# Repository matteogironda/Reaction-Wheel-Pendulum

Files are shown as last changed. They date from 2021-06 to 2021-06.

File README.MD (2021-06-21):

# This project is intended to be fully open source. For questions feel free to contact me at girondamatteo@gmail.com

## Mechanical Design:

All SolidWorks CAD files are found in the CAD folder. All 3D printed parts are in the STL subdriectory.

### CAD Assembly:

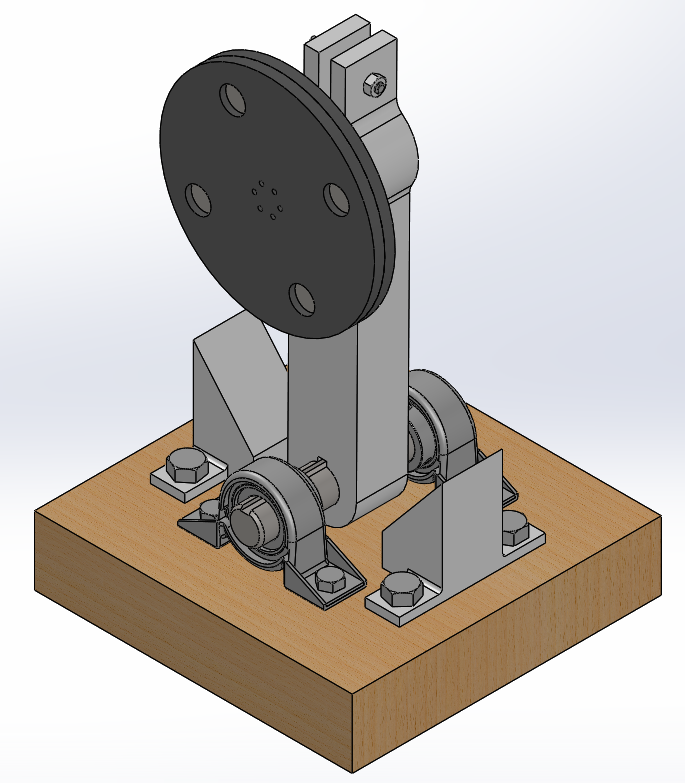
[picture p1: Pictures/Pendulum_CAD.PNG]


### Bill of Materials:

> •	Raspberry Pi (any version with 20 GPIO pins)

> •	Raspberry Pi HAT for DC Motors (https://learn.adafruit.com/adafruit-dc-and-stepper-motor-hat-for-raspberry-pi)

> •	12V DC motor (mine has a max speed of 500 rpm and 1A max)

> •	BNO08x sensor (https://learn.adafruit.com/adafruit-9-dof-orientation-imu-fusion-breakout-bno085/arduino)

> •	9x9x2 in wooden block

> •	Motor attachment to fit with motor shaft (mine had a 6mm shaft https://www.amazon.com/gp/product/B00B887FX8/ref=ppx_yo_dt_b_asin_title_o04_s00?ie=UTF8&psc=1)

> •	Screws for motor attachment (mine were 6x #4-40 x1”)

> •	Keyed 1” Diameter shaft 6” in length

> •	Key (mine was ¼” x ¼”, 1-3/4” long, depends on the keyway of the shaft)

> •	2x Mounted ball bearings for shaft (mounts could theoretically be 3D printed, I bought mine with mounting points)

> •	¼” – 20 thread. 1-1/2” long thumb screw and nut (this is to clamp the motor to the top of the arm)

> •	Self tapping screws for the bearing mounts and side supports (I ended up going with a ½” size, 1-1/2” long; definitely an overkill and not as easy to drive into wood. Make sure you have the appropriate drive bits and socket adapters)

> •	Steel (or metal with similar density) ring (https://www.ebay.com/itm/203450660510)

> •	Access to a 3D printer, soldering iron, appropriate DC power supplies (separate for Pi and motor), connectors, drill, foam, tape.  

### Front View of Pendulum:
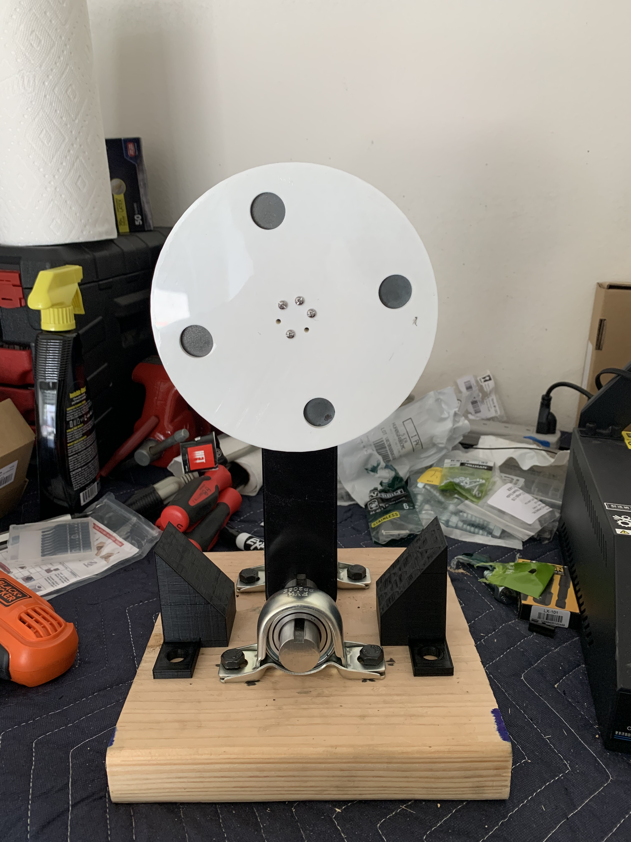
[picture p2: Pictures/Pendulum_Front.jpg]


### Side View of Pendulum:
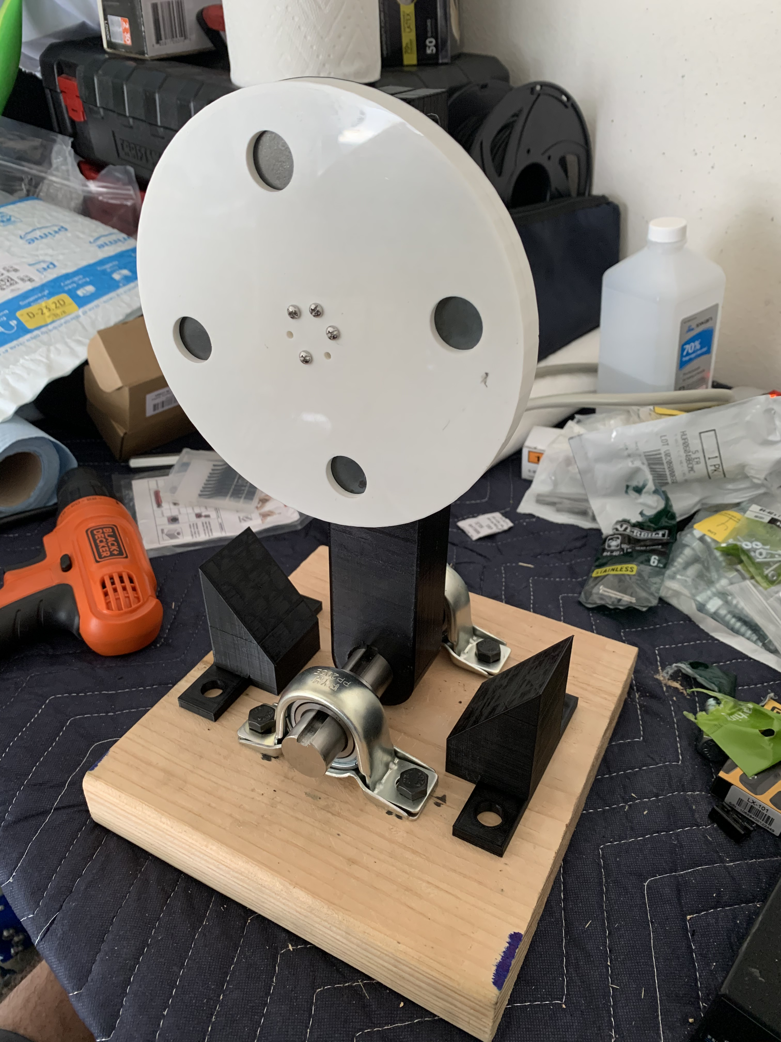
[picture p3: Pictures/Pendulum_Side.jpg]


The mechanical design was inspred by https://www.researchgate.net/publication/331271615_Design_Modeling_and_Control_of_a_Reaction_Wheel_Balanced_Inverted_Pendulum and its authors. 

## Controller

The idea is to send a PWM signal to the motor to rotate the reaction wheel against the motion of the pendulum arm. Gains are tuned to adjust the needed voltage input based on the state vector of the arm. States are updated from the IMU in the feedback loop. The control input becomes saturated at 12V and -12V.

A simulation of the equations of motion and state vector algebra is found in simulation.py. The simulation allows you to change starting conditions and gains, and outputs control effort and states. 

## Notes

I am using UART communication over I2C because the BNO08x series has clock stretching issues when interfacing with the default I2C bus of the pi. This can be worked around by using different SCL and SDA pins on the GPIO that use hardware clock stretching instead of software clock stretching (see https://github.com/adafruit/Adafruit_CircuitPython_BNO08x/issues/7). I found that it's just simpler to use UART for this application, as the motor driver is already using the pi's default I2C bus.

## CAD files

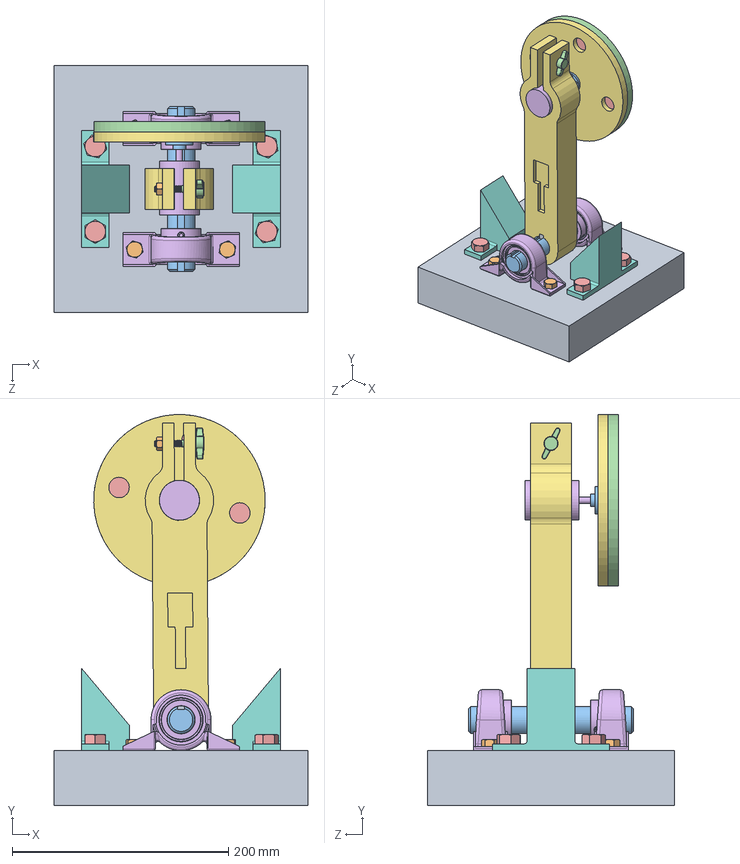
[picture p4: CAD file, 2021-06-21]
CAD/Assembly.SLDASM
235.0 x 361.9 x 228.6 mm
Key
Motor_Nut
Shaft
Thumb_Screw
Wood_Screw x 4
Bearing x 2
Pendulum_Arm
Side_Support x 2
Wooden_Block
Bearing_Wood_Screw x 4
Motor_Mount
Outside_Wheel_Mount
Reaction_Wheel
Motor
Motor_Side_Wheel_Mount

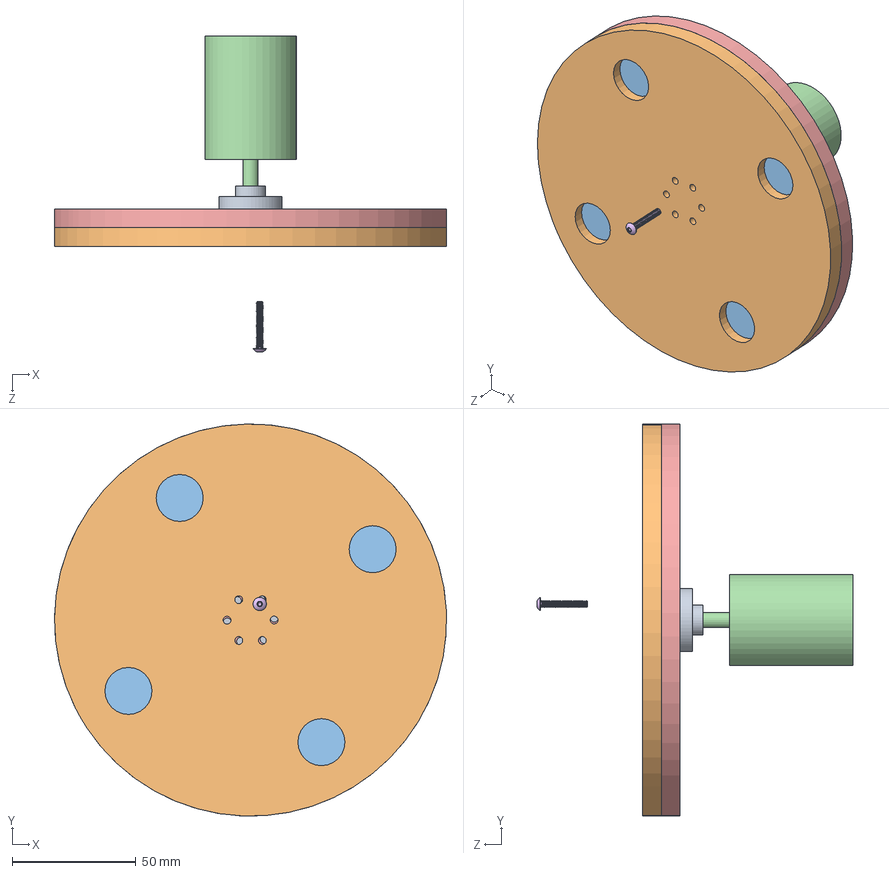
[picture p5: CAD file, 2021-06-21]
CAD/Wheel_Assembly.SLDASM
158.7 x 158.7 x 128.0 mm
Motor_Mount
Outside_Wheel_Mount
Reaction_Wheel
Motor
Motor_Side_Wheel_Mount
Wheel_Screw

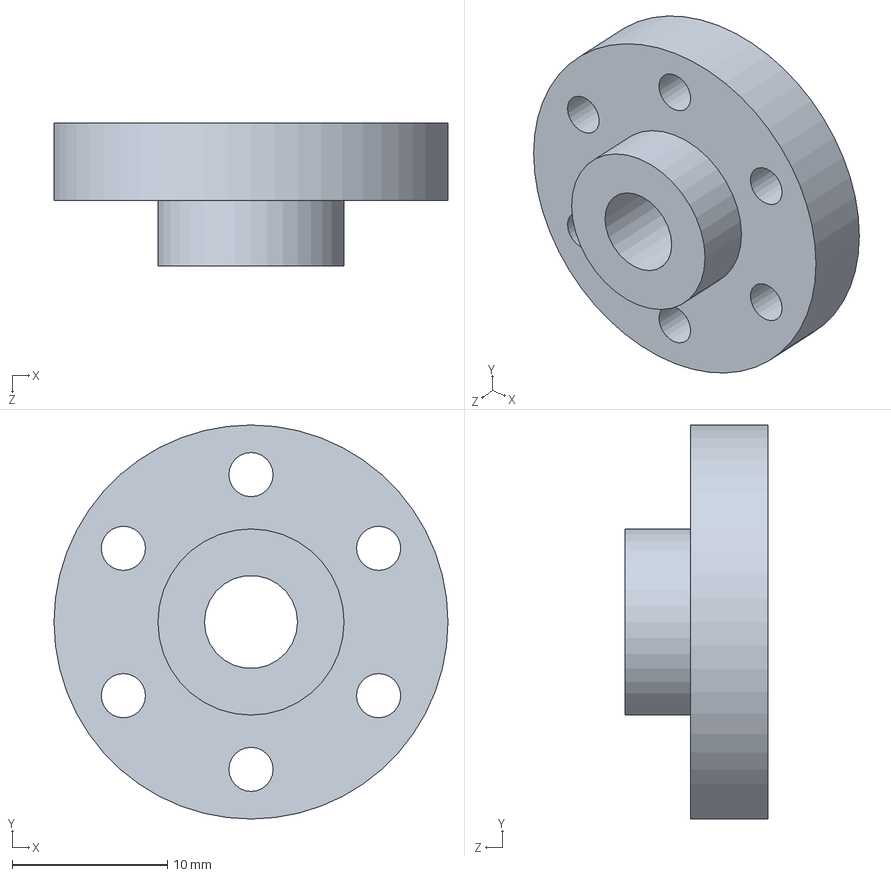
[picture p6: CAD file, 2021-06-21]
CAD/Motor_Mount.SLDPRT
25.4 x 25.4 x 9.20 mm

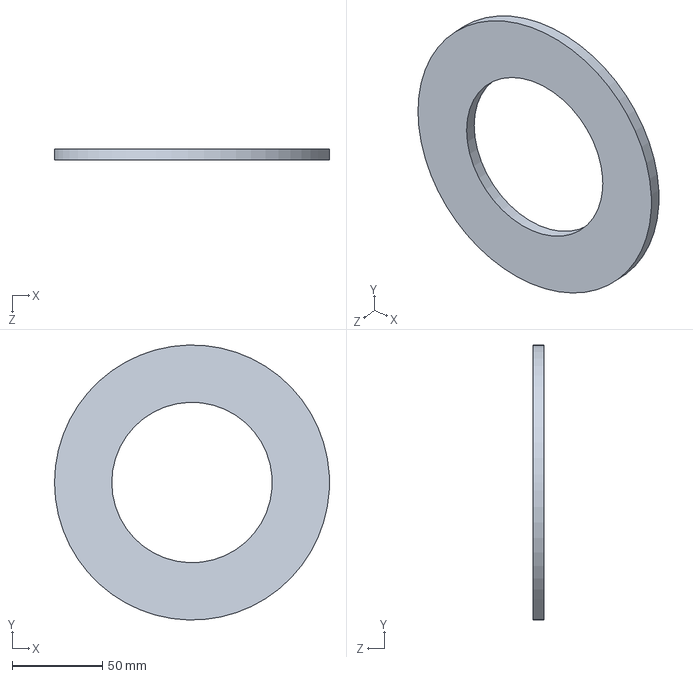
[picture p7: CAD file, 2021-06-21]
CAD/Reaction_Wheel.SLDPRT
152.4 x 152.3 x 6.35 mm

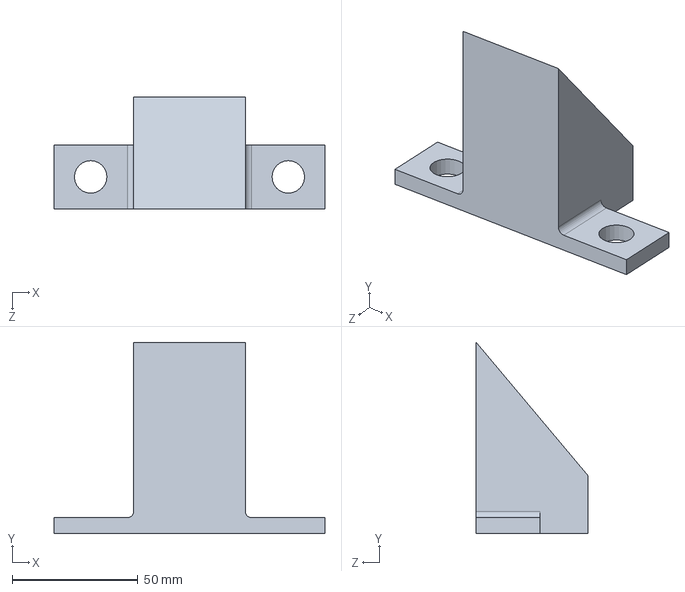
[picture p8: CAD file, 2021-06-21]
CAD/Side_Support.SLDPRT
108.0 x 76.2 x 44.5 mm

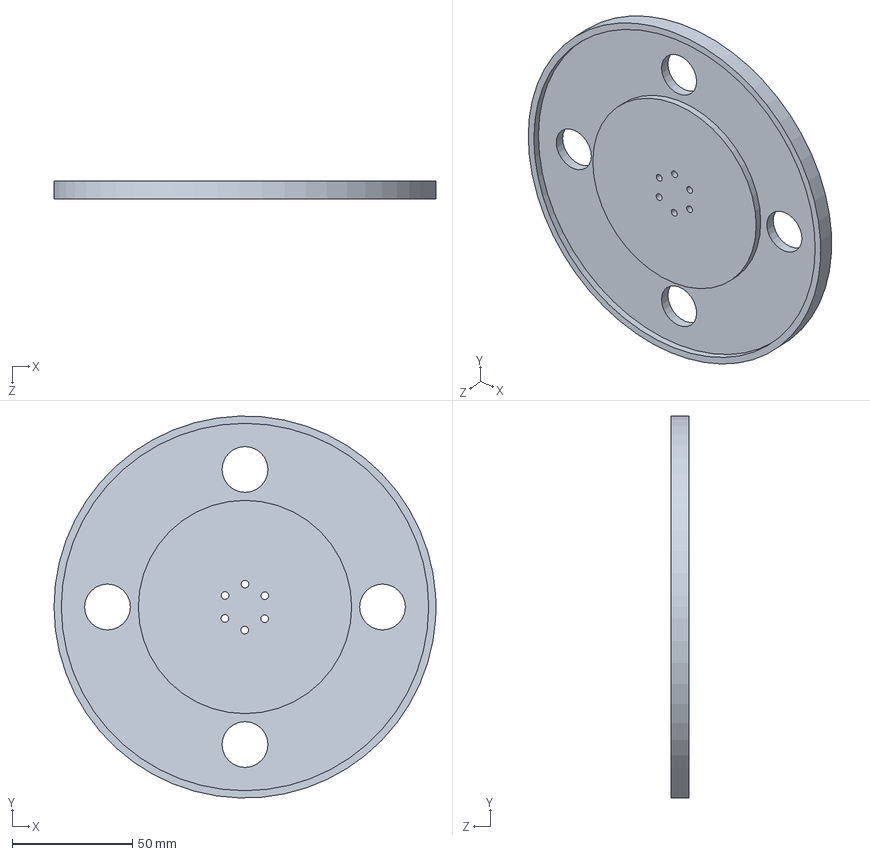
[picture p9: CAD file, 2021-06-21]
CAD/Motor_Side_Wheel_Mount.SLDPRT
158.8 x 158.7 x 7.62 mm

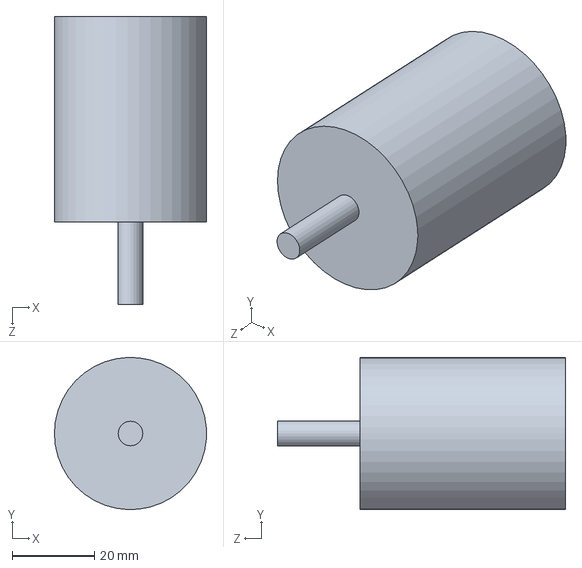
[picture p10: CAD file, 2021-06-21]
CAD/Motor.SLDPRT
37.0 x 37.0 x 70.0 mm

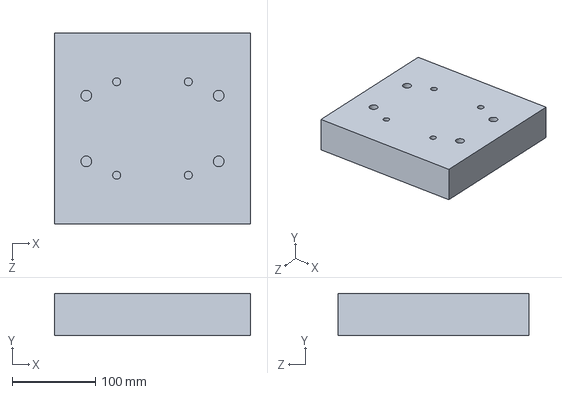
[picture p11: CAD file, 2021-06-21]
CAD/Wooden_Block.SLDPRT
235.0 x 50.8 x 228.6 mm

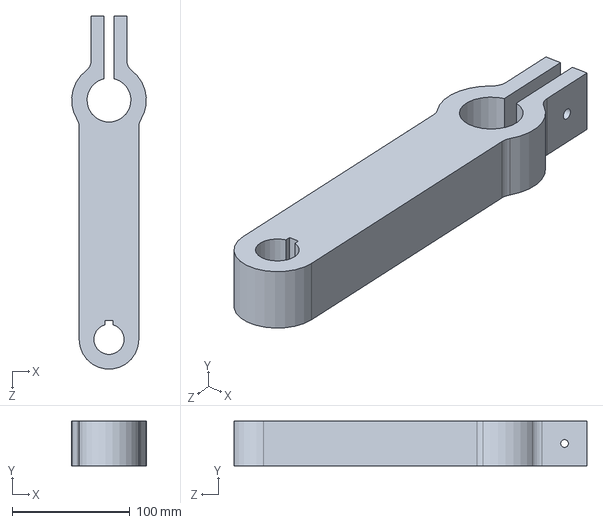
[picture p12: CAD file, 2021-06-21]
CAD/Pendulum_Arm.SLDPRT
63.3 x 38.1 x 299.9 mm

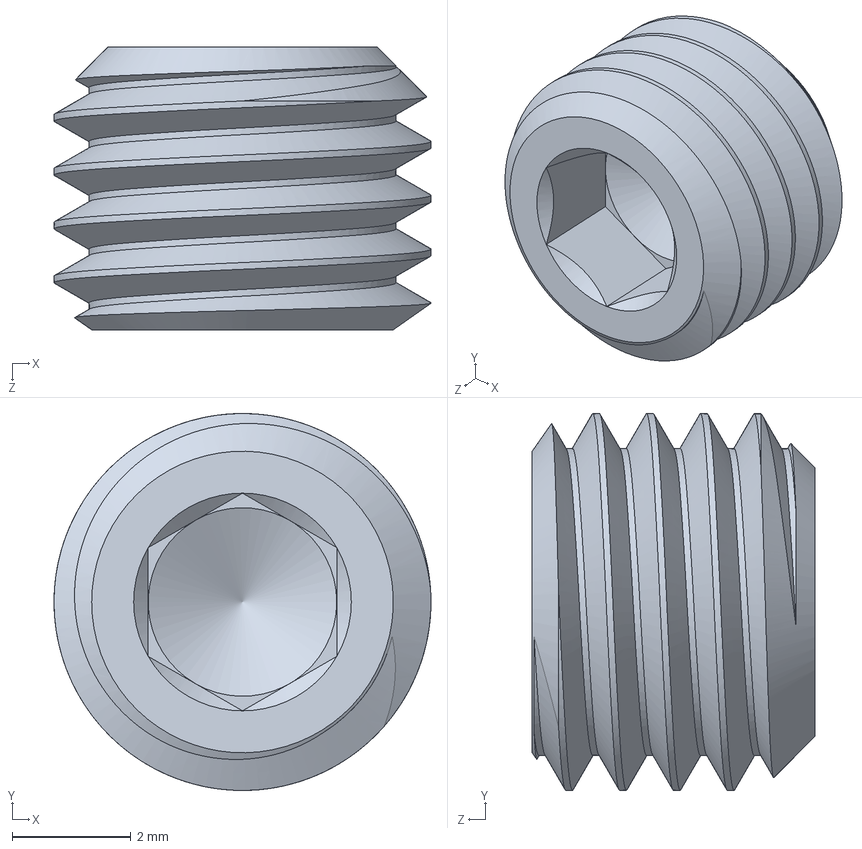
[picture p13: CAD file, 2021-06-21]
CAD/McMaster/Set_Screw.SLDPRT
6.35 x 6.35 x 4.76 mm

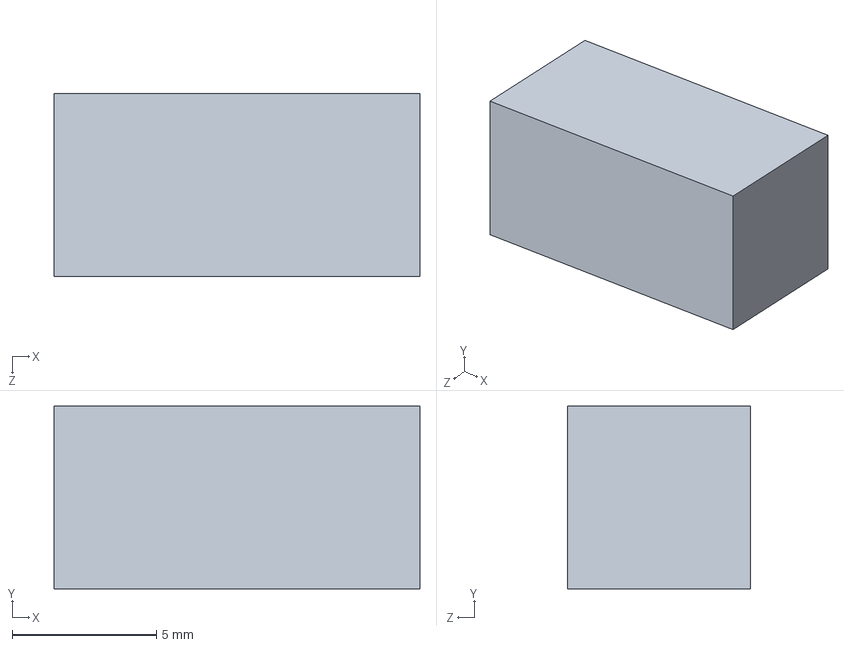
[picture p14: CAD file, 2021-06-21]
CAD/McMaster/Key.SLDPRT
12.7 x 6.35 x 6.35 mm

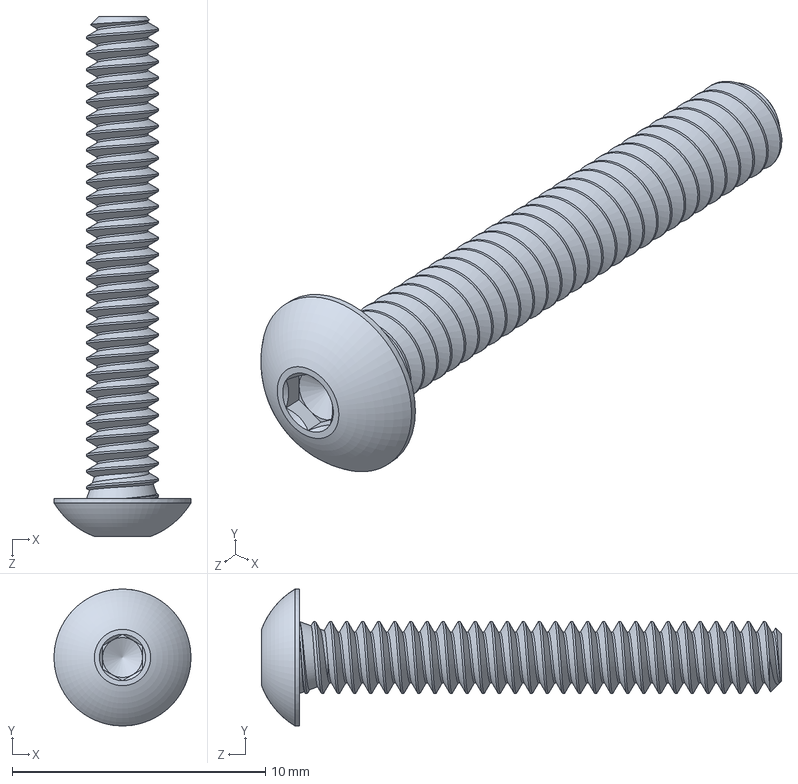
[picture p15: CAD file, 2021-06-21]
CAD/McMaster/Wheel_Screw.SLDPRT
5.41 x 5.41 x 20.5 mm

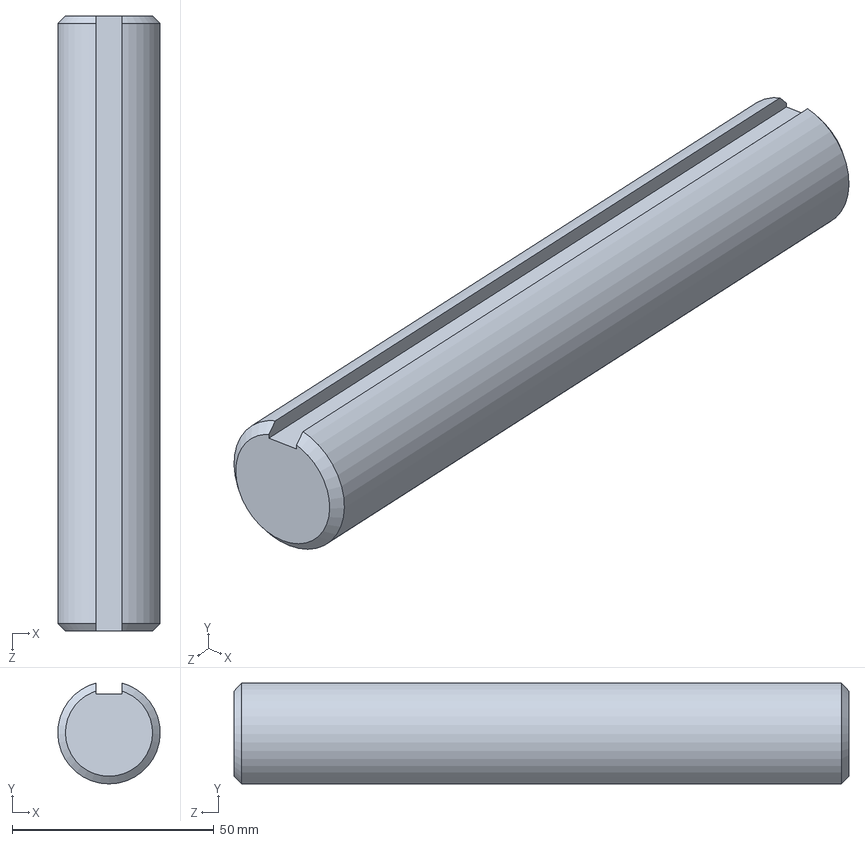
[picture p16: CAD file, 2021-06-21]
CAD/McMaster/Shaft.SLDPRT
25.4 x 25.0 x 152.4 mm

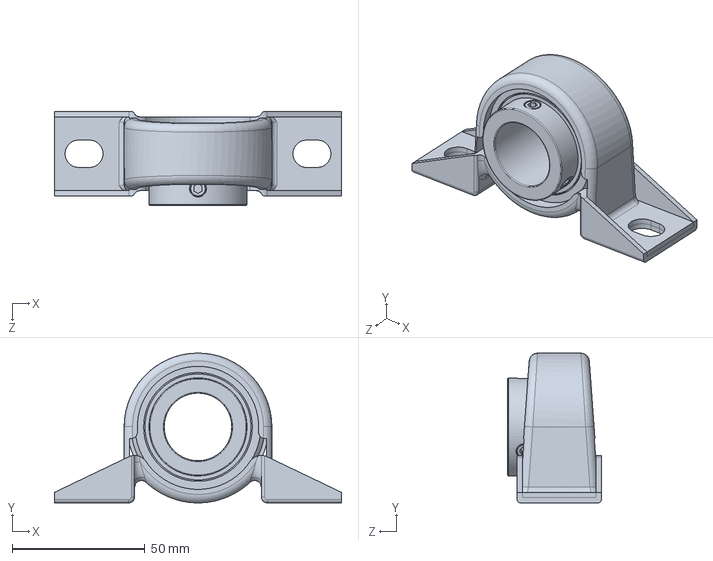
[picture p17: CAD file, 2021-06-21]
CAD/McMaster/Bearing.SLDPRT
108.0 x 56.4 x 35.3 mm

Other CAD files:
CAD/Outside_Wheel_Mount.SLDPRT
CAD/McMaster/Wood_Screw.SLDPRT
CAD/McMaster/Thumb_Screw.SLDPRT
CAD/McMaster/Motor_Nut.SLDPRT
CAD/McMaster/Bearing_Wood_Screw.SLDPRT
CAD/STL/Motor_Side_Wheel_Mount.STL
CAD/STL/Outside_Wheel_Mount.STL
CAD/STL/Pendulum_Arm.STL
CAD/STL/Side_Support.STL

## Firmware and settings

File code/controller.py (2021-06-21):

import numpy as np
import time
import board
from adafruit_motorkit import MotorKit
import busio
import board
import digitalio
import serial
from adafruit_bno08x_rvc import BNO08x_RVC

def uart_test():
    print('hello')
    uart = serial.Serial("/dev/serial0", 115200)
    rvc = BNO08x_RVC(uart)
    i = 0
    while i < 100:
        uart = serial.Serial("/dev/serial0", 115200)
        rvc = BNO08x_RVC(uart)
        print('in loop...')
        yaw, pitch, roll, x_accel, y_accel, z_accel = rvc.heading
        print("Yaw: %2.2f Pitch: %2.2f Roll: %2.2f Degrees" % (yaw, pitch, roll))
        print("Acceleration X: %2.2f Y: %2.2f Z: %2.2f m/s^2" % (x_accel, y_accel, z_accel))
        print("")
        time.sleep(0.1)
        i += 1
        
try:
    kit = MotorKit()
    print('[CHECK     ]  [MOTOR DRIVER]')
except Exception as e:
    print('[     ERROR]  [MOTOR DRIVER]',e)

class controller:
    
    def __init__(self):
        
        self.state = []
        self.state_collection = {'x1':[], 'x2':[],'x3':[],'x4':[], 'u':[]}
        self.ref = float(0)
        self.gain = 1.2 # 12V / 10 deg/s = 1.2 
        self.k_motor = 10 #?
        self.kit = kit
        self.saturated_voltage = 12 #V

    def turn_off(self):

        print('TURNING OFF')
        self.kit.motor1.throttle = 0

    def deinit(self):

        pass

    #Read current sensor values
    def get_state(self):
        
        try:
            uart = serial.Serial("/dev/serial0", 115200)
            rvc = BNO08x_RVC(uart)
            gyro_z, gyro_x, gyro_y, x_accel, y_accel, z_accel = rvc.heading
            time.sleep(0.5)

            print('gyro: %0.3f'%(gyro_z))
            state = [0, gyro_z, 0, self.ref - 0]

            return state

        except Exception as e:
            self.turn_off()
            print('ERROR in get_state: ',e)
            
    #Handle situation where control input is too large for max motor voltage 
    def saturate_handle(self, signal):

        if signal > 1:
            print('Saturated Signal...Desaturating from %0.3f V to 12V' %(signal*self.saturated_voltage))
            return 1 

        elif signal < -1:
            print('Saturated Signal...Desaturating from %0.3f V to -12V' %(signal*self.saturated_voltage))
            return -1

        else:
            return signal

    #Store state values into lists
    def update_state_collection(self, state):

        self.state_collection['x1'].append(state[0])
        self.state_collection['x2'].append(state[1])
        self.state_collection['x3'].append(state[2])
        self.state_collection['x4'].append(state[3])

    #Apply control law and actuate motor
    def control(self, state):
        
        u = self.gain * state[1] / self.saturated_voltage
        print('u: %0.3f'%(u)) 
        u = self.saturate_handle(u)

        state[2] = u * self.k_motor
        self.update_state_collection(state)
              
        try:
            self.kit.motor1.throttle = u

        except Exception as e:
            self.turn_off()
            print('ERROR in control: ', e)

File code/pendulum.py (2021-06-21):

import numpy as np
from scipy.integrate import odeint
from matplotlib import pyplot as plt

### Inverted pendulum dynamics simulation ###

class Pendulum:

    def __init__(self, prop):

        self.m = prop['m']
        self.g = prop['g']
        self.arm = prop['arm']
        self.R = prop['R']
        self.I = prop['I']
        self.k_m = prop['k_m']
        self.I_m = prop['I_m']
        self.t = prop['t']
        self.L = prop['L']
        self.x0 = prop['x0']
        
    def odes(self, x, t):

        r = 0
        x1 = x[0]; x2 = x[1]; x3 = x[2]; x4 = x[3]
        u = np.matmul(self.L,x)

        x1_dot = x2 
        x2_dot = self.m*self.g*self.arm/self.I * x1 + self.k_m**2/(self.I*self.R) * x3 - u * -self.k_m/(self.I*self.R)
        x3_dot = -self.k_m**2/(self.I_m*self.R) * x3 - u * -self.k_m/(self.I_m*self.R)
        x4_dot = r - x1 

        return [x1_dot, x2_dot, x3_dot, x4_dot]

    def controller(self):
        
        u = -np.matmul(self.L, self.x) 

        return u

    def solve(self):

        x = odeint(self.odes, self.x0, self.t)
        theta = x[:,0]
        theta_dot = x[:,1]
        omega = x[:,2]

        u = []
        for i in range(len(self.t)):
            u.append(np.matmul(-self.L, x[i,:]))

        print(u[1])
        # plot the results
        plt.plot(self.t,theta)
        plt.plot(self.t,theta_dot)
        #plt.plot(self.t,omega)
        #plt.plot(self.t,u)

        plt.legend(['theta','theta_dot','omega'])
        plt.show()

    def animate(self):
        pass

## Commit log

2021-06-21 pendulum.py and simulation.py are intended for simulation. main.py and controller.py are for controlling the wheel.
2021-06-21 CAD files
    McMaster folder has files of parts ordered from McMaster Carr.
    STL folder has parts to slice to gcode and 3D print.
    Assembly.SLDASM should just open if you downloaded every part under the same path to its directory.
    [Assembly.SLDASM, Bearing.SLDPRT, Bearing_Wood_Screw.SLDPRT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]
2021-06-21 Changed from I2C to UART
